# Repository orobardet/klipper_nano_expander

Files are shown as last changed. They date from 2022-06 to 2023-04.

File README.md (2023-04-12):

# Klipper Nano Expander

An Arduino Nano Shield to use with Klipper 3D printer firmware, as a auxiliary MCU.

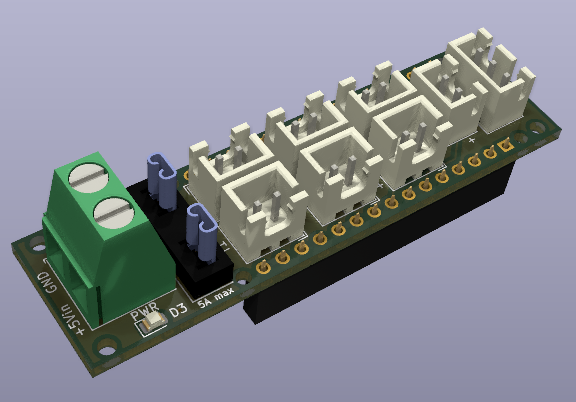
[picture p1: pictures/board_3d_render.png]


## Features

- Only require an Arduino Nano
- +5V optional external power supply with fuse
  - Connected to the Arduino Nano 5V
  - Only required if you need more than 500mA power, else the Nano power supply should be enough
- x4 temperature sensors (or any analog device as input)
- x3 PWM mosfet driven port (or any PWM controlled device as output)
- x1 Neopixel (external 5V power supply needed)

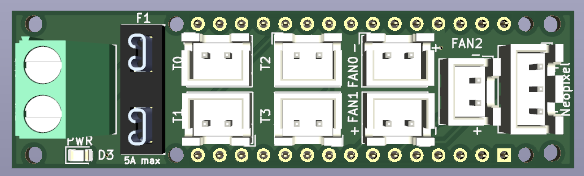
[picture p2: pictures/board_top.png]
  
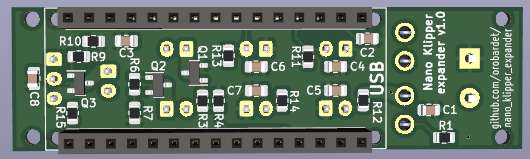
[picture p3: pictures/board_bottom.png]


- [Schematic](Schematic.pdf)
- [Mechanical drawing](Dimensions.pdf)

Source files:
- Kicad 6 project, schematic, PCB and library
- [CAD files](CAD/), including .STEP and Fusion 360 source

## Why

- Adds more temperature sensors and fan controllers
- Drives 5V fans
- Drives a 5V Neopixel without a level shifter
- Arduino nano are cheap
- Arduino nano are easy to source
- A lot of people (including me) have some in their drawers
- This board only have simple components easy to find
- Small footprint
- Does not need any hardware interaction to flash (no boot jumper or boot button to press)

## How to build

[production directory](production/) contains Gerber file and BOM + Position file for JLCPCB assembly.

If you use JLC PCB to produce and assemble your board, configure PCBA for the bottom side, where most of the SMD
component are placed.  
You'll have to solder by yourself the power indicator LED on the front of the board. It's a 0805, that can be soldered by hand.  
However this LED is not mandatory for the board to work, you can skip soldering it if you want.  
You'll also have to source and solder all the other non-SMD components:
- x2 15 pins female dupont header for the Arduino Nano (or directly the male pin of the Nano, which is not recommended)
- x1 [Keystone 3544-2 mini fuse holder](https://www.digikey.com/en/products/detail/keystone-electronics/3544-2/316029)
- x7 2 pins JST connector (FANx and THx headers)
- x1 3 pins JST connector (Neopixel headers)
- x1 screw terminal pitch 5.08mm for power in

### BOM

- [Interactive BOM](http://htmlpreview.github.io/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)
- [CSV](Klipper_nano_expander-BOM.csv) or [XLSX](Klipper_nano_expander-BOM.xlsx) BOM

Ref                | Qty | Value          | Description                                              | Soldering     | Footprint         | LCSC Ref
-------------------|-----|----------------|----------------------------------------------------------|---------------|-------------------|------------
C1, C8             |   2 | 10uF	          | Unpolarized ceramic capacitor                            | PCBA          | 0805              | [C17024](https://lcsc.com/product-detail/Multilayer-Ceramic-Capacitors-MLCC-SMD-SMT_Samsung-Electro-Mechanics-CL21A106KPFNNNE_C17024.html)
C2, C3             |   2 | 0.1uF          | Unpolarized ceramic capacitor                            | PCBA          | 0805              | [C49678](https://lcsc.com/product-detail/Multilayer-Ceramic-Capacitors-MLCC-SMD-SMT_YAGEO-CC0805KRX7R9BB104_C49678.html)
C4, C5, C6, C7     |   4 | 4.7uF          | Unpolarized ceramic capacitor                            | PCBA          | 0805              | [C1779](https://lcsc.com/product-detail/Multilayer-Ceramic-Capacitors-MLCC-SMD-SMT_Samsung-Electro-Mechanics-CL21A475KAQNNNE_C1779.html)
Q1, Q2, Q3         |   3 | IRLML6344TRPBF | MOSFET N-CH 30V 5A SOT23                                 | PCBA          | SOT-23            | [C20917](https://lcsc.com/product-detail/MOSFETs_Alpha-Omega-Semicon-AO3400A_C20917.html)
R1                 |   1 | 1K             | Resistor                                                 | PCBA          | 0805              | [C17513](https://lcsc.com/product-detail/Chip-Resistor-Surface-Mount_UNI-ROYAL-Uniroyal-Elec-0805W8F1001T5E_C17513.html)
R3, R6, R9, R15    |   4 | 100            | Resistor                                                 | PCBA          | 0805              | [C17408](https://lcsc.com/product-detail/Chip-Resistor-Surface-Mount_UNI-ROYAL-Uniroyal-Elec-0805W8F1000T5E_C17408.html)
R4, R7, R10        |   3 | 10K            | Resistor                                                 | PCBA          | 0805              | [C17414](https://lcsc.com/product-detail/Chip-Resistor-Surface-Mount_UNI-ROYAL-Uniroyal-Elec-0805W8F1002T5E_C17414.html)
R11, R12, R13, R14 |   4 | 4.7K           | Resistor                                                 | PCBA          | 0805              | [C17673](https://lcsc.com/product-detail/Chip-Resistor-Surface-Mount_UNI-ROYAL-Uniroyal-Elec-0805W8F4701T5E_C17673.html)
D3                 |   1 | Any color      | LED                                                      | PCBA          | 0805              | [C84256](https://lcsc.com/product-detail/Light-Emitting-Diodes-LED_Foshan-NationStar-Optoelectronics-NCD0805R1_C84256.html)
A1                 |   1 |                | Arduino Nano v3.x                                        | Hand-soldered |                   |
A1-a, A1-b         |   2 |                | 15 pins female dupont header + 15 mins mal dupont header | Hand-soldered | P2.54             |
F1                 |   1 | Fuse           | Mini fuse holder + 2A or 5A mini fuse                    | Hand-soldered | 3544-2_FuseHolder | 	
J1                 |   1 |                | Screw terminal 2 pins P5.08mm                            | Hand-soldered | P5.08mm           | 
FAN0, FAN1, FAN2   |   3 |                | JST 2 pins P2.54mm                                       | Hand-soldered | P2.54             | 
T0, T1, T2, T3     |   4 |                | JST 2 pins P2.54mm                                       | Hand-soldered | P2.54             | 
Neopixel           |   1 |                | JST 3 pins P2.54mm                                       | Hand-soldered | P2.54             | 

## How to use

**ONLY** use **5V** power supply! The Vin of the bord is connected to the 5V of the Arduino Nano, with no protection:  
any power >5V may fry your Nano, and any power <5V may fry you power supply.

Powering on Vin with an external 5V power supply is only necessary if you device draw more current than the Nano can provide (800mA theorically, 
but with so many Nano clone out there it's safer to stick to 500mA max).
- If you only plug temperature sensors, the Nano power supply should be enough
- If you drive a fan, I'd better power the board with external power supply (most fan draws more then 500mA when they start)
- If you drive an neopixel, **powering the board with external power supply is highly recommended**

In doubt, power the board. You should already have a 5V power source if you use Klipper, to power the Pi.

FANx header are mosfet PWM output, driving the ground:
- You can use them for anything else than FAN, like LED, heater, etc. Just stick to 1A per output max.
- If the fan or whatever you drive is not 5V, just connect its ground to the Klipper Nano Expander, and its +V to any compatible power source, **but ensure that other PSU's ground is connected to the board ground!**.

### Software configuration

Once built and connected to your Klipper host, use the provided [Klipper config file](config/nano_klipper_expander.cfg).  

You need at least to set the `serial` path in the `[mcu ...]` of the provided klipper configuration file.  
To find the serial of your Arduino Nano:
- BEFORE connecting the Nano with USB on the Raspberry Pi, connect to the Pi using SSH and run the command `ls /dev/serial/by-id/`. Note the result.
- Connect the Nano with USB on the Pi, wait a few seconds for the Pi to detect the USB device, and re-run the same command as before.
- A new "file" should be there, looking like `usb-1a86_USB2.0-Serial-if00-port0`: it represents your Arduino Nano
- Change the `serial` setting value in the Klipper configuration using the full path to the serial file. e.g.: `serial: /dev/serial/by-id/usb-1a86_USB2.0-Serial-if00-port0`

Here is the pin mapping for reference:
- TH0: PC0
- TH1: PC1
- TH2: PC2
- TH3: PC3
- FAN0: PB1
- FAN1: PD5
- FAN2: PD3
- Neopixel Data: PD6

The configuration file must be included in some way into the main `printer.cfg` config filr of Klipper.

### Flashing firmware

To flash the firmware, you do not need to have the configuration file ready, but you need:
- The Nano connected to the Raspberry Pi
- The path of the serial representing the Nano on the Pi (see previous section)
- Klipper installed on the Pi
- AVR compilation package installed on the Rapsberry Pi hosting Klipper: `sudo apt install gcc-avr avr-libc avrdude binutils-avr`

To flash the Nano with Klipper:

- Connect to the Pi using SSH.
- Create a `klipper_config` directory in you home directory, if it not exists already: `mkdir -p ~/klipper_config`.
- Go the the directory containing klipper (usually: `cd ~/klipper`).
- Run `make clean KCONFIG_CONFIG=~/klipper_config/config.arduinonano`.
- Run `make menuconfig KCONFIG_CONFIG=~/klipper_config/config.arduinonano` and configure as followed, and then save'n'quit:  
  - _Enable extra low-level configuration options_: NOT checked
  - _Micro-controller Architecture_: `Atmega AVR`
  - _Processor model_: `atmega328p`   
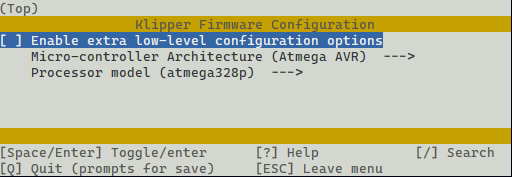
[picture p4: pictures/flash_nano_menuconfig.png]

- Run `make KCONFIG_CONFIG=~/klipper_config/config.arduinonano` to build the firmware.  
  **Note:** If the firmware compilation fails with errors like `'.data' is not within region 'data'`, you may sufffer a known bug with AVR toolchain on Debian Bullseye (check your linux distribution codename with `lsb_release -a`). If so, you can try [a workaround describe here to install a previous and non-buggy AVR toolchain](https://github.com/Klipper3d/klipper/issues/4938#issuecomment-1094246978). Once installed, re-roll the current procedure from the `make clean` step (a reboot of the Pi may be usefull between new toolchain installation and the retry).
- **Stop Klipper** if it's running (usually: `sudo systemctl stop klipper`)
- Run `make flash KCONFIG_CONFIG=~/klipper_config/config.arduinonano FLASH_DEVICE=/dev/serial/by-id/usb-1a86_USB2.0-Serial-if00-port0`, _**replacing the `FLASH_DEVICE=` value with the full path of you Nano on your Pi!**_ This will flash the firmware to the Arduino Nano.
- Start Klipper (usually: `sudo systemctl start klipper`)

If no error occurs, Klipper's firmware is now loaded into the Arduino Nano.  
You can now configure Klipper to use the Nano Expander.

### Mounting

x2 3D printable mounts are provided (STL files):
- [without mounting holes](STL/nano_expander_mount.stl): lower footprint, but require some tape (like VHB tape) to secure the mount on a flat surface.
- [with mounting holes](STL/nano_expander_mount_with_holes.stl): a wider mount with 4 mounting holes, to secure the mount with M3 screws. Screws position and distance can be found in [dimension drawing](Dimensions.pdf).

Both mounts require x4 M2x3mm screw to secure the board to the mount.

## Compatibility

Aside from Arduino Nano and its clone, this board _may_ be compatible with other MCU boards using the same form factor than the Arduino Nano, and a compatible pinout.

- [Cytron Maker Nano RP2040](config/rp2040_klipper_expander.cfg): flashing the firmware is a bit different, as it is based on the Raspberry Pi RP2040 MCU rather than an ATMega MCU. 

## Credit

Inspired by [STM32-Klipper-Expander](https://github.com/VoronDesign/Voron-Hardware/tree/master/Klipper_Expander) by Voron Design Team.  
Temperature sensors and FAN output of Klipper Nano Expander are a copy of those of STM32-Klipper-Expander.  
The Cytron Maker Nano RP2040 config is a contribution of **tehmaze** (#2).

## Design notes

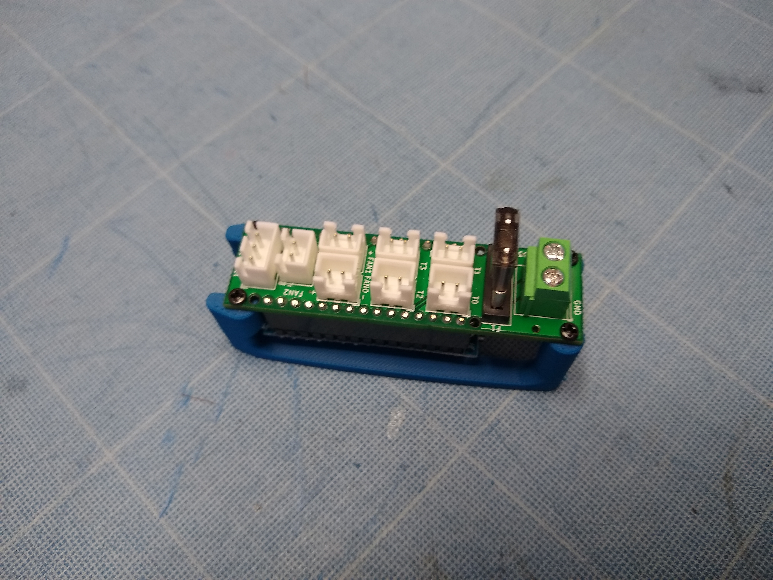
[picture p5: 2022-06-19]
pictures/klipper_nano_expander_real_full.jpg

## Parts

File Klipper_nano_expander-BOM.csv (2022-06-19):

Ref | Qty | Value | Description | Footprint | LCSC Ref
A1 | 1 |  | Arduino Nano v3.x
A1-a, A1-b | 2 |  | 15 pins female dupont header + 15 mins mal dupont header
C1, C8 | 2 | 10uF | Unpolarized ceramic capacitor | 0805 | C17024
C2, C3 | 2 | 0.1uF | Unpolarized ceramic capacitor | 0805 | C49678
C4, C5, C6, C7 | 4 | 4.7uF | Unpolarized ceramic capacitor | 0805 | C1779
D3 | 1 | Any color | LED | 0805 | C84256
F1 | 1 | Fuse | Mini fuse holder + 2A or 5A mini fuse | 3544-2_FuseHolder
Q1, Q2, Q3 | 3 | IRLML6344TRPBF | MOSFET N-CH 30V 5A SOT23 | SOT-23 | C20917
R1 | 1 | 1K | Resistor | 0805 | C17513
R3, R6, R9, R15 | 4 | 100 | Resistor | 0805 | C17408
R4, R7, R10 | 3 | 10K | Resistor | 0805 | C17414
R11, R12, R13, R14 | 4 | 4.7K | Resistor | 0805 | C17673
J1 | 1 |  | Screw terminal 2 pins P5.08mm | P5.08mm
FAN0, FAN1, FAN2 | 3 |  | JST 2 pins P2.54mm | P2.54
T0, T1, T2, T3 | 4 |  | JST 2 pins P2.54mm | P2.54
Neopixel | 1 |  | JST 3 pins P2.54mm | P2.54

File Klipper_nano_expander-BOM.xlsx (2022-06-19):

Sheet: Klipper nano expander BOM
Ref | Qty | Value | Description | Footprint | LCSC Ref
A1 | 1 |  | Arduino Nano v3.x
A1-a, A1-b | 2 |  | 15 pins female dupont header + 15 mins mal dupont header
C1, C8 | 2 | 10uF | Unpolarized ceramic capacitor | 0805 | C17024
C2, C3 | 2 | 0.1uF | Unpolarized ceramic capacitor | 0805 | C49678
C4, C5, C6, C7 | 4 | 4.7uF | Unpolarized ceramic capacitor | 0805 | C1779
D3 | 1 | Any color | LED | 0805 | C84256
F1 | 1 | Fuse | Mini fuse holder + 2A or 5A mini fuse | 3544-2_FuseHolder
Q1, Q2, Q3 | 3 | IRLML6344TRPBF | MOSFET N-CH 30V 5A SOT23 | SOT-23 | C20917
R1 | 1 | 1K | Resistor | 0805 | C17513
R3, R6, R9, R15 | 4 | 100 | Resistor | 0805 | C17408
R4, R7, R10 | 3 | 10K | Resistor | 0805 | C17414
R11, R12, R13, R14 | 4 | 4.7K | Resistor | 0805 | C17673
J1 | 1 |  | Screw terminal 2 pins P5.08mm | P5.08mm
FAN0, FAN1, FAN2 | 3 |  | JST 2 pins P2.54mm | P2.54
T0, T1, T2, T3 | 4 |  | JST 2 pins P2.54mm | P2.54
Neopixel | 1 |  | JST 3 pins P2.54mm | P2.54

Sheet: Klipper nano expander
Ref,"Qnty","Value","Cmp name","Footprint","Description","Vendor"
A1, ,"1","Arduino_Nano_v3.x","Arduino_Nano_v3.x","Module:Arduino_Nano_WithMountingHoles","Arduino Nano v3.x",""
C1, C8, ,"2","10uF","C","Capacitor_SMD:C_0805_2012Metric","Unpolarized capacitor",""
C2, C3, ,"2","0.1uF","C","Capacitor_SMD:C_0805_2012Metric","Unpolarized capacitor",""
C4, C5, C6, C7, ,"4","4.7uF","C","Capacitor_SMD:C_0805_2012Metric","Unpolarized capacitor",""
D3, ,"1","LED","LED","LED_SMD:LED_0805_2012Metric","Light emitting diode",""
F1, ,"1","Fuse","Fuse","local:3544-2_FuseHolder","Fuse",""
FAN0, FAN1, FAN2, ,"3","Conn_01x02","Conn_01x02","Connector_JST:JST_XH_B2B-XH-A_1x02_P2.50mm_Vertical","Generic connector, single row, 01x02, script generated (kicad-library-utils/schlib/autogen/connector/)",""
H1, H2, H3, H4, ,"4","MountingHole","MountingHole","MountingHole:MountingHole_2mm","Mounting Hole without connection",""
J1, ,"1","+5Vin","Screw_Terminal_01x02","TerminalBlock_Phoenix:TerminalBlock_Phoenix_MKDS-1,5-2-5.08_1x02_P5.08mm_Horizontal","Generic screw terminal, single row, 01x02, script generated (kicad-library-utils/schlib/autogen/connector/)",""
J2, ,"1","Conn_01x03","Conn_01x03","Connector_JST:JST_XH_B3B-XH-A_1x03_P2.50mm_Vertical","Generic connector, single row, 01x03, script generated (kicad-library-utils/schlib/autogen/connector/)",""
Q1, Q2, Q3, ,"3","IRLML6344TRPBF","IRLML6344TRPBF","Package_TO_SOT_SMD:SOT-23","MOSFET N-CH 30V 5A SOT23",""
R1, ,"1","1K","R","Resistor_SMD:R_0805_2012Metric","Resistor",""
R3, R6, R9, R15, ,"4","100","R","Resistor_SMD:R_0805_2012Metric","Resistor",""
R4, R7, R10, ,"3","10K","R","Resistor_SMD:R_0805_2012Metric","Resistor",""
R11, R12, R13, R14, ,"4","4.7K","R","Resistor_SMD:R_0805_2012Metric","Resistor",""
T0, T1, T2, T3, ,"4","Conn_01x02","Conn_01x02","Connector_JST:JST_XH_B2B-XH-A_1x02_P2.50mm_Vertical","Generic connector, single row, 01x02, script generated (kicad-library-utils/schlib/autogen/connector/)",""

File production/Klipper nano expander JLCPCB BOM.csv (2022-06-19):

Comment | Designator | Footprint | LCSC
Arduino_Nano_v3.x | A1 | Module:Arduino_Nano_WithMountingHoles
10uF | C1,C8 | Capacitor_SMD:C_0805_2012Metric | C17024
0.1uF | C2,C3 | Capacitor_SMD:C_0805_2012Metric | C49678
4.7uF | C4,C5,C6,C7 | Capacitor_SMD:C_0805_2012Metric | C1779
LED | D3 | LED_SMD:LED_0805_2012Metric | C84256
Fuse | F1 | local:3544-2_FuseHolder
Conn_01x02 | FAN0,T0,FAN1,T1,FAN2,T2,T3 | Connector_JST:JST_XH_B2B-XH-A_1x02_P2.50mm_Vertical
MountingHole | H1,H2,H3,H4 | MountingHole:MountingHole_2mm
+5Vin | J1 | TerminalBlock_Phoenix:TerminalBlock_Phoenix_MKDS-1,5-2-5.08_1x02_P5.08mm_Horizontal
Conn_01x03 | J2 | Connector_JST:JST_XH_B3B-XH-A_1x03_P2.50mm_Vertical
IRLML6344TRPBF | Q1,Q2,Q3 | Package_TO_SOT_SMD:SOT-23 | C20917
1K | R1 | Resistor_SMD:R_0805_2012Metric | C17513
4.7K | R11,R12,R13,R14 | Resistor_SMD:R_0805_2012Metric | C17673
100 | R3,R6,R9,R15 | Resistor_SMD:R_0805_2012Metric | C17408
10K | R4,R7,R10 | Resistor_SMD:R_0805_2012Metric | C17414

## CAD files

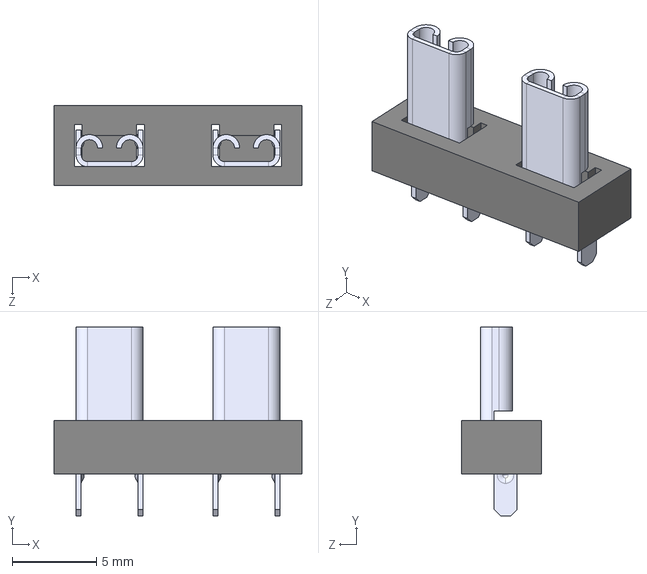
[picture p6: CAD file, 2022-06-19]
3d_models/3544-2_FuseHolder.STEP
14.7 x 11.2 x 4.75 mm

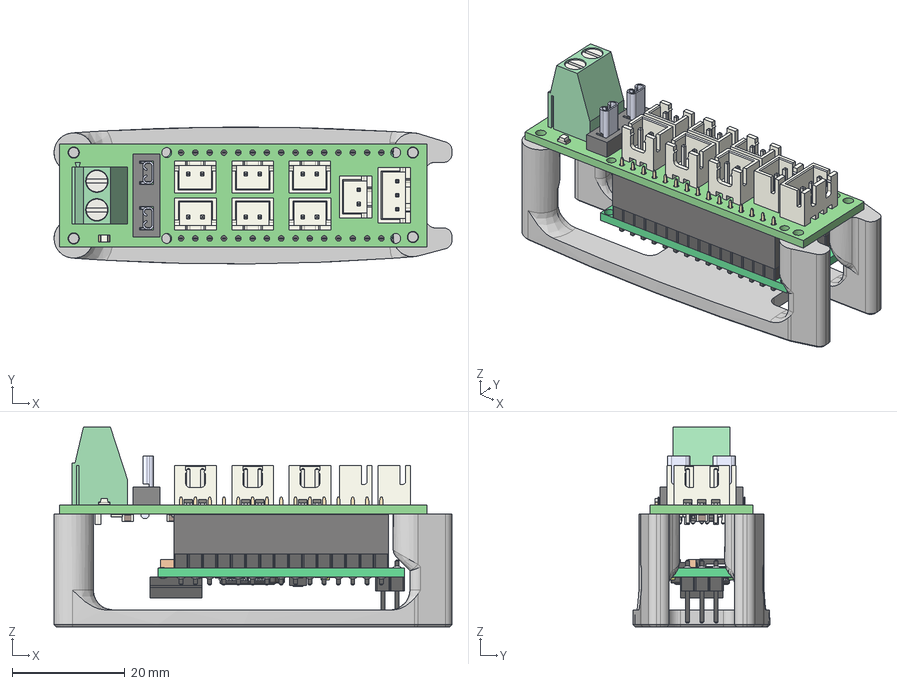
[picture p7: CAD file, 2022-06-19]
CAD/Klipper Nano expander mount.step
70.6 x 24.3 x 35.5 mm
Klipper nano expander PCB
switch
Led x 3
Led (1)
Pin x 21
chip1
USB
Crystal
Pin (1) x 15
Res x 5
cap x 2
Chip
respack x 2
diode
vreg
nano_expander_mount

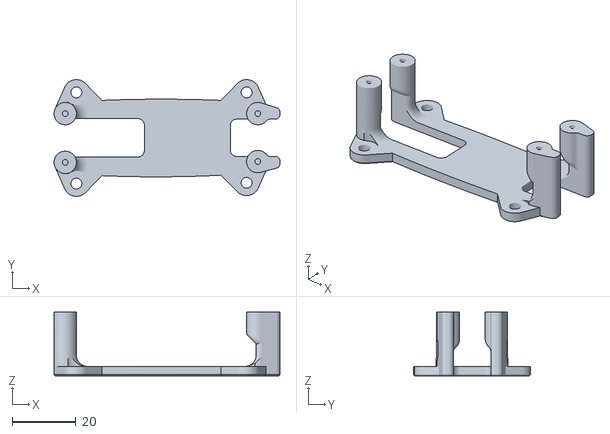
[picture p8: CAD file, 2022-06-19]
STL/nano_expander_mount_with_holes.stl
70.6 x 36.5 x 20.0

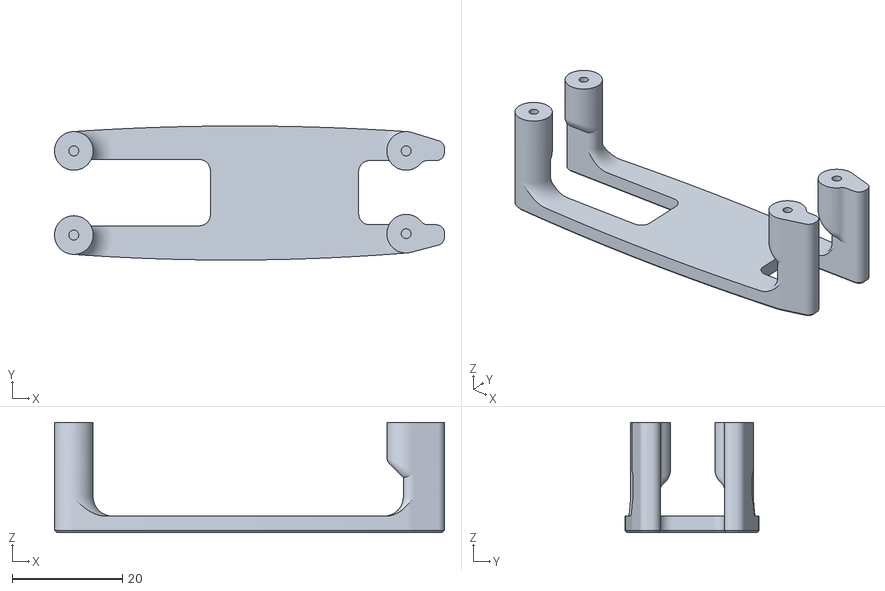
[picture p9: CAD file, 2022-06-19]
STL/nano_expander_mount.stl
70.6 x 24.3 x 20.0

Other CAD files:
CAD/Klipper Nano expander mount.f3z

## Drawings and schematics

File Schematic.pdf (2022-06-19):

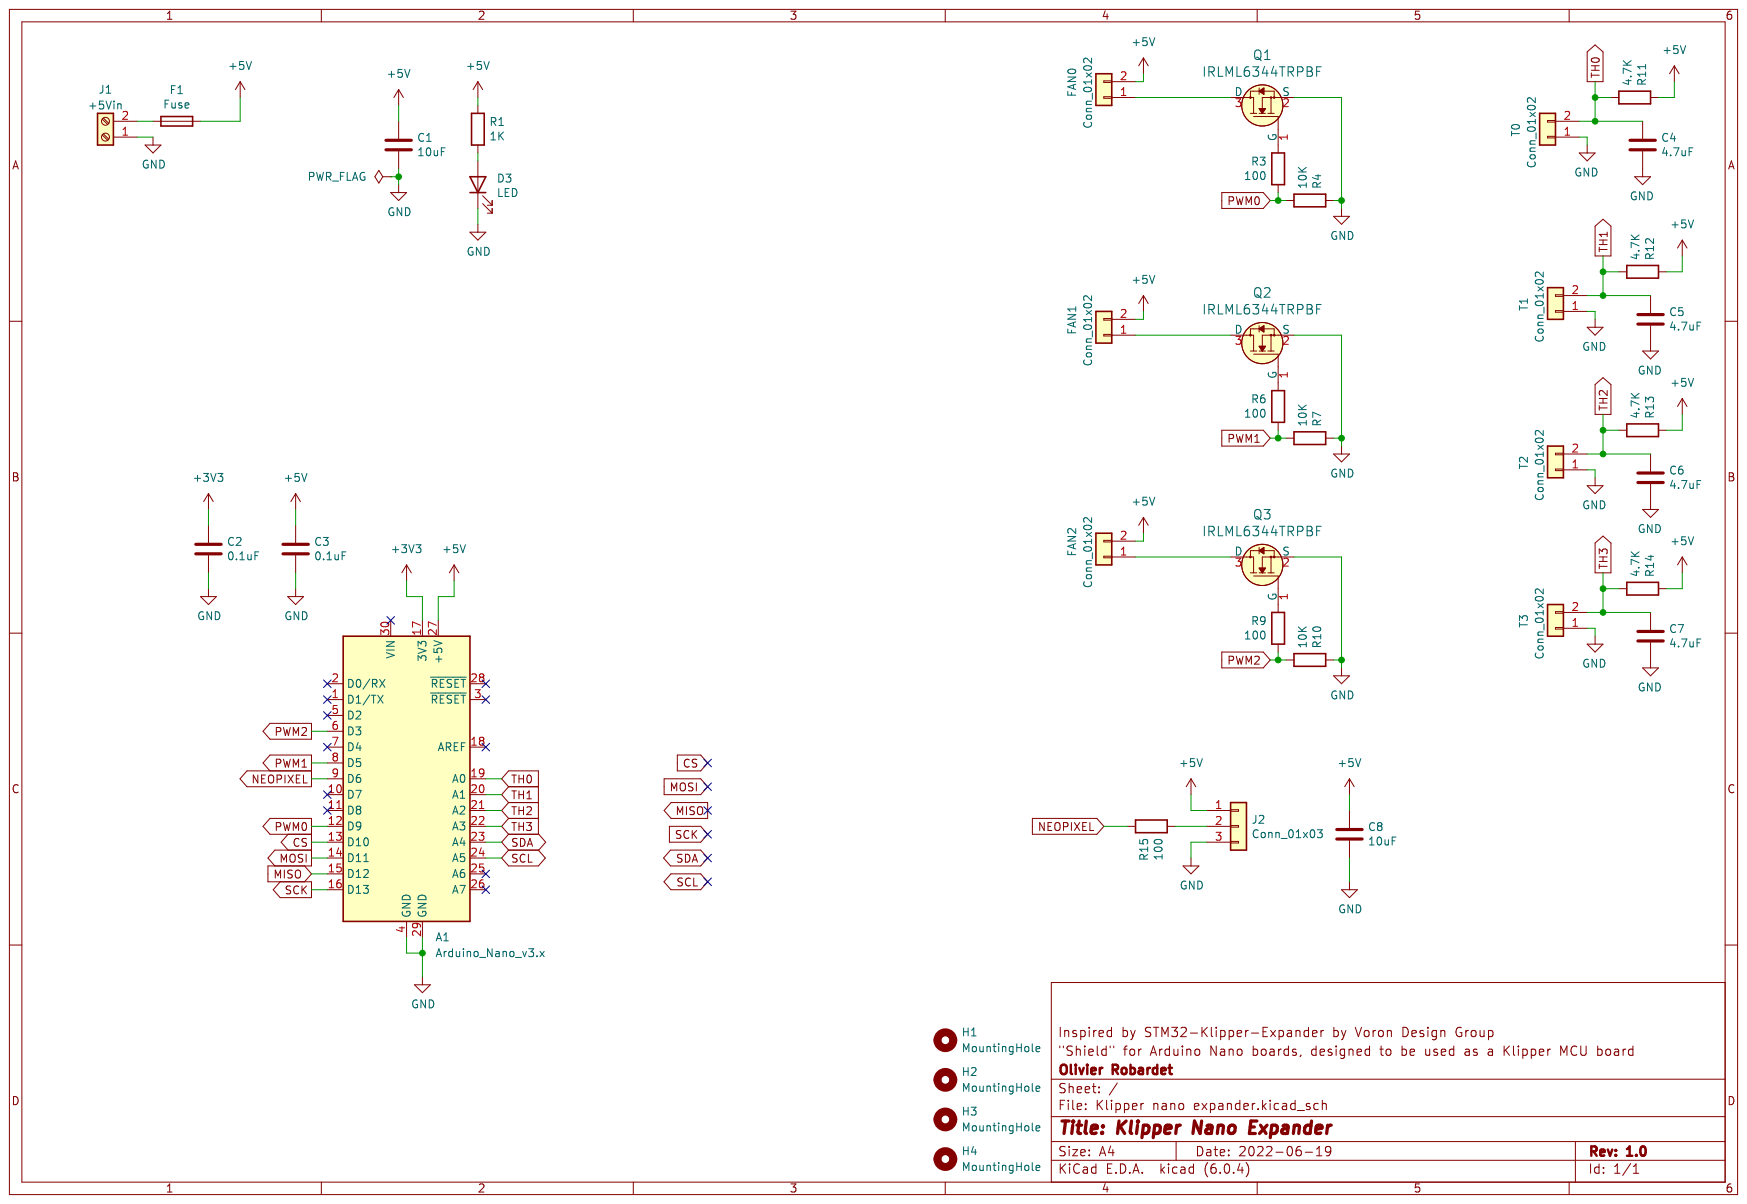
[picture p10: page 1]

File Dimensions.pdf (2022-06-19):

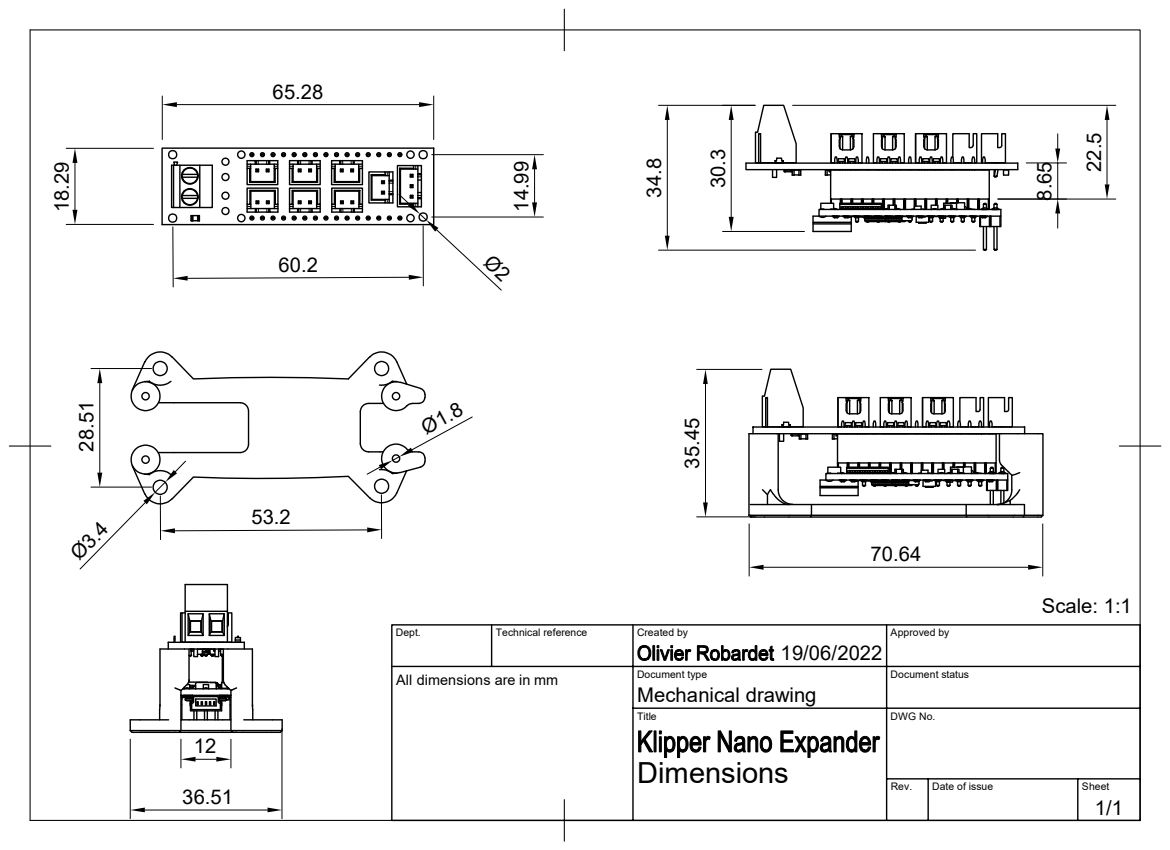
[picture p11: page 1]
Dept.; Technical reference; Created by; Approved by Document type; Document status Title; DWG No. Rev.; Date of issue; Sheet Mechanical drawing 19/06/2022; 1/1 Dimensions ⁶⁵.28

Ø2 Scale: 1:1 All dimensions are in mm

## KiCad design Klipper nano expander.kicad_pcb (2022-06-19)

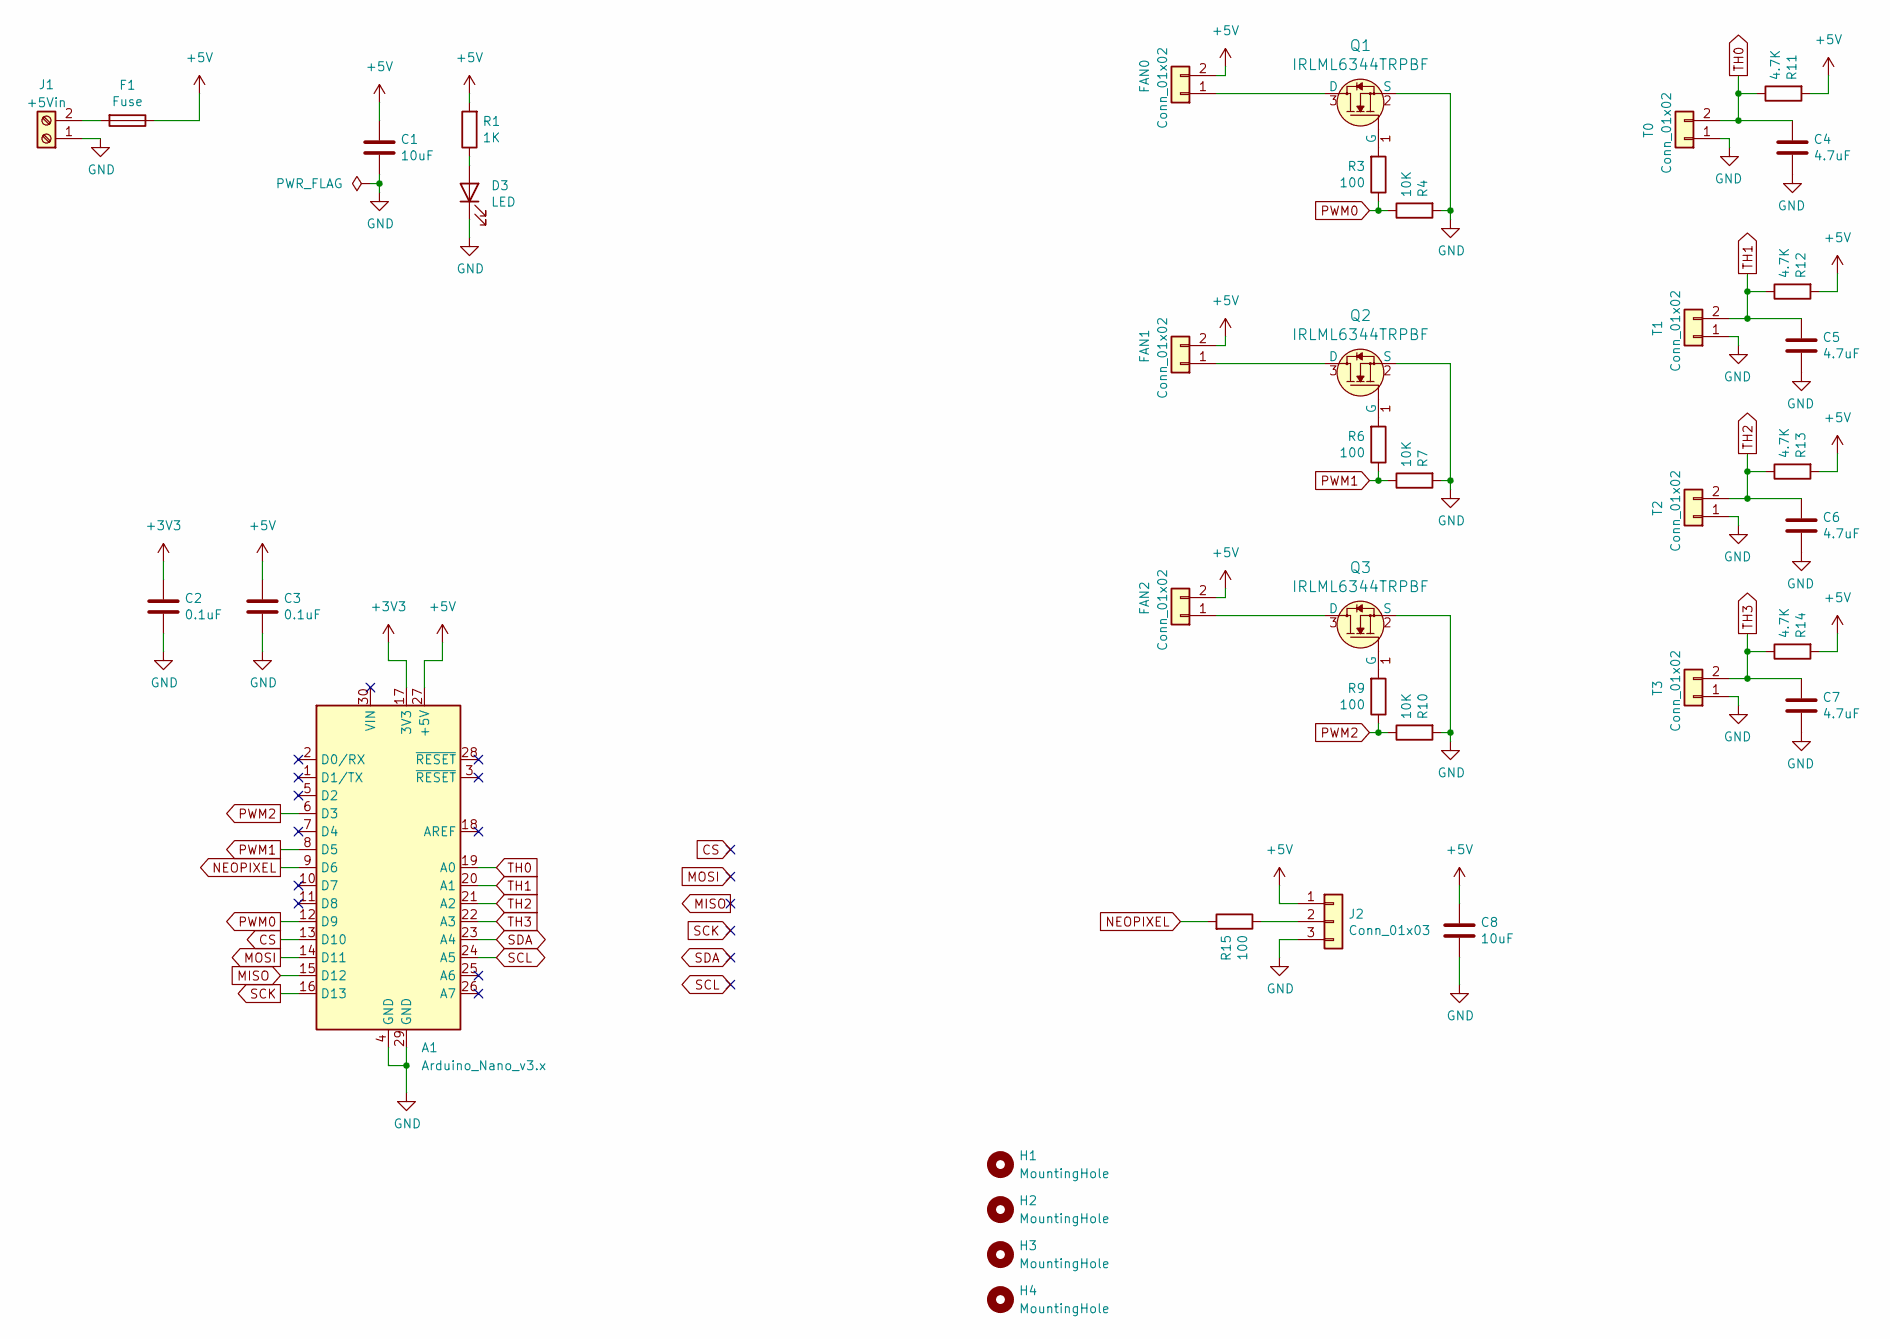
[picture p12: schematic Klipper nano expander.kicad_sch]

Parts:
A1: Arduino_Nano_v3.x; Arduino_Nano_WithMountingHoles
C1, C8: 10uF; C_0805_2012Metric; MPN CL21A106KPFNNNE; LCSC C17024
C2, C3: 0.1uF; C_0805_2012Metric; MPN CC0805KRX7R9BB104; LCSC C49678
C4, C5, C6, C7: 4.7uF; C_0805_2012Metric; MPN CC0805KKX5R8BB475; LCSC C1779
D3: LED; LED_0805_2012Metric; MPN 17-215SURC/S530-A2/TR8; LCSC C84256
F1: Fuse; 3544-2_FuseHolder
FAN0, FAN1, FAN2: Conn_01x02; JST_XH_B2B-XH-A_1x02_P2.50mm_Vertical
H1, H2, H3, H4: MountingHole; MountingHole_2mm
J1: +5Vin; TerminalBlock_Phoenix_MKDS-1,5-2-5.08_1x02_P5.08mm_Horizont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
J2: Conn_01x03; JST_XH_B3B-XH-A_1x03_P2.50mm_Vertical
Q1, Q2, Q3: IRLML6344TRPBF; SOT-23; MPN IRLML6344TRPBF; Digi-Key_PN IRLML6344TRPBFCT-ND
R1: 1K; R_0805_2012Metric; MPN RC0805JR-071KL; LCSC C17513
R3, R6, R9, R15: 100; R_0805_2012Metric; MPN RC0805JR-07100RL; LCSC C17408
R4, R7, R10: 10K; R_0805_2012Metric; MPN RC0805JR-0710KL; LCSC C17414
R11, R12, R13, R14: 4.7K; R_0805_2012Metric; MPN RC0805JR-074K7L; LCSC C17673
T0, T1, T2, T3: Conn_01x02; JST_XH_B2B-XH-A_1x02_P2.50mm_Vertical

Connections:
+3V3: A1.17 (3V3), C2.2
+5V: A1.27 (+5V), C1.2, C3.2, C8.2, F1.1, FAN0.2, FAN1.2, FAN2.2, J2.1, R1.2, R11.2, R12.2, R13.2, R14.2
CS: A1.13 (D10)
GND: A1.4 (GND), A1.29 (GND), C1.1, C2.1, C3.1, C4.1, C5.1, C6.1, C7.1, C8.1, D3.1 (K), J1.1, J2.3, Q1.2 (S), Q2.2 (S), Q3.2 (S), R4.2, R7.2, R10.2, T0.1, T1.1, T2.1, T3.1
MISO: A1.15 (D12)
MOSI: A1.14 (D11)
NEOPIXEL: A1.9 (D6), R15.2
unnamed: D3.2 (A), R1.1
unnamed: F1.2, J1.2
unnamed: FAN0.1, Q1.3 (D)
unnamed: FAN1.1, Q2.3 (D)
unnamed: FAN2.1, Q3.3 (D)
unnamed: J2.2, R15.1
unnamed: Q1.1 (G), R3.2
unnamed: Q2.1 (G), R6.2
unnamed: Q3.1 (G), R9.2
PWM0: A1.12 (D9), R3.1, R4.1
PWM1: A1.8 (D5), R6.1, R7.1
PWM2: A1.6 (D3), R9.1, R10.1
SCK: A1.16 (D13)
SCL: A1.24 (A5)
SDA: A1.23 (A4)
TH0: A1.19 (A0), C4.2, R11.1, T0.2
TH1: A1.20 (A1), C5.2, R12.1, T1.2
TH2: A1.21 (A2), C6.2, R13.1, T2.2
TH3: A1.22 (A3), C7.2, R14.1, T3.2

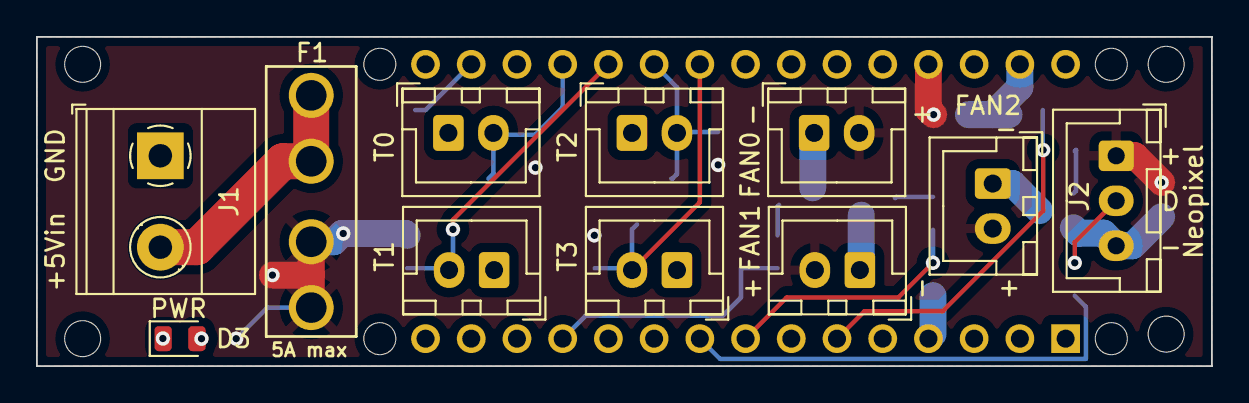
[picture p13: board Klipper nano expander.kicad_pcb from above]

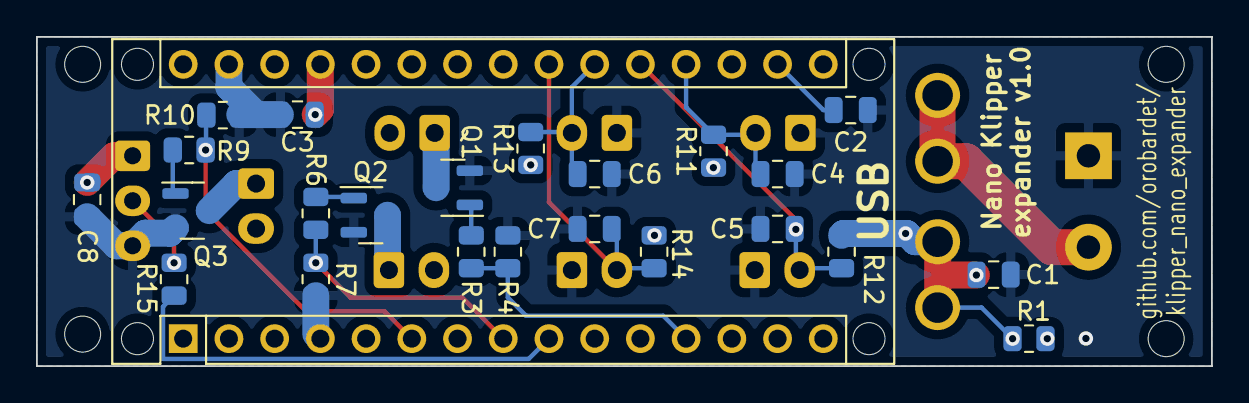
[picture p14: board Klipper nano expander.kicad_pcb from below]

Board: 2 copper layers, 65.3 x 18.3 mm, 39 parts (24 on the bottom side), 20 nets.

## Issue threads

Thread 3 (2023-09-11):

Only 5V fan?

za-x-az, 2023-09-11:
Is it correct that this is only for 5V fans?

I was looking for just a board like this, but for 12/24v fans.

orobardet, 2023-09-12:
Hi,
Yes, it's 5V only, there is no regulator on the board. It was design for this purpose: having auxiliary Kilipper MCUs capable of driving 5V devices.

For 12/24V, you may want to use the [Klipper Expander](https://github.com/VoronDesign/Voron-Hardware/tree/master/Klipper_Expander).

za-x-az, 2023-09-12:
Sadly I'm looking for something more or less like your board, but for
12/24V :)
Thx for the fast answer i will keep looking

On Tue, 12 Sept 2023 at 08:32, Olivier Robardet ***@***.***>
wrote:

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

--
M.v.h. / Best Regards

Andreas L. Rasmussen

Closed 2024-05-17.

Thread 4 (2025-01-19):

Collect2 error

jStrahan73, 2025-01-19:
When I try to make the elf file I get this error

Collect2: error: ld returned 1 exit status
Makefile 73 out/klipper.elf error 1

orobardet, 2025-01-21:
Hi @jStrahan73,

On what hardware and Operating System are you trying to build the firmware? If using a debian-based OS bookworm or latter, did you see in the README and apply the workaround for the AVR toolchain? (https://github.com/Klipper3d/klipper/issues/4938#issuecomment-1094246978)

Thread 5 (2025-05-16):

Thermistor Pullup resistor should connect to +3.3V, not 5V

kpt-smirk, 2025-05-16:
The pullup resistor (4k7ohm) should connect to the 3v3 Power level, not to the  5v
I use the board with the maker nano RP2040 and i read completely wrong temperatures,

kpt-smirk, 2025-05-16:
In the scheme it's R11 ... R14

orobardet, 2025-05-16:
Hi.
Thanks for your report, but this board was designed on purpose for **5V** Arduino Nano, which use an ATmega328.
So, it's expected it does not work correctly on a 3.3V RP2040 MCU. It's by design.

Closed 2025-05-16.

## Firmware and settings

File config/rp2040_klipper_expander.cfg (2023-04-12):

# Configuration for the Cytron Maker Nano RP2040
#
# This board has two NeoPixels on GPIO11, a beeper on GPIO22 and a bunch of 
# individually controllable LEDs on GPIO12-15.

[mcu expander]
serial: /dev/serial/by-id/usb-Klipper_rp2040_XXXXXXXXXXXX-if00

[neopixel expander_leds]
pin:         expander:gpio11
chain_count: 2
color_order: GRB

[output_pin expander_beeper]
pin:         expander:gpio22
pwm:         True
value:       0
shutdown_value: 0
cycle_time:  0.001

[temperature_sensor expander]
sensor_type: temperature_mcu
sensor_mcu:  expander

[temperature_sensor TH0]
sensor_pin:  expander:gpio26
sensor_type: Generic 3950

#[temperature_sensor TH1]
#sensor_pin:  expander:gpio27
#sensor_type: Generic 3950

#[temperature_sensor TH2]
#sensor_pin:  expander:gpio28
#sensor_type: Generic 3950

#[temperature_sensor TH3]
#sensor_pin:  expander:gpio29
#sensor_type: Generic 3950

[fan_generic FAN0]
pin:         expander:gpio9
max_power:   1.0

#[fan_generic FAN1]
#pin:         expander:gpio5
#max_power:   1.0
#
#[fan_generic FAN2]
#pin:         expander:gpio3
#max_power:   1.0

[gcode_macro M300]
gcode:
  # Use a default 1kHz tone if S is omitted.
    {% set S = params.S|default(1000)|int %}
    # Use a 10ms duration is P is omitted.
    {% set P = params.P|default(100)|int %}
    SET_PIN PIN=expander_beeper VALUE=0.5 CYCLE_TIME={ 1.0/S if S > 0 else 1 }
    G4 P{P}
    SET_PIN PIN=expander_beeper VALUE=0

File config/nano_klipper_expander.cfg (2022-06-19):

[mcu nano_expander]
# CHANGE THE SERIAL!
serial: /dev/serial/by-id/usb-xxx
restart_method: arduino

# TH0
[temperature_sensor TH0]
sensor_pin: nano_expander:PC0
sensor_type: Generic 3950

# # TH1
# [temperature_sensor TH1]
# sensor_pin: nano_expander:PC1

# # TH2
# [temperature_sensor TH2]
# sensor_pin: nano_expander:PC2

# # TH3
# [temperature_sensor TH3]
# sensor_pin: nano_expander:PC3

# FAN0
[fan_generic FAN0]
pin: nano_expander:PB1
max_power: 1.0

# # FAN1
# [fan_generic FAN1]
# pin: nano_expander:PD5
# max_power: 1.0

# # FAN2
# [fan_generic FAN2]
# pin: nano_expander:PD3
# max_power: 1.0

# Neopixel
[neopixel nano_expander_neopixel]
pin: nano_expander:PD6
chain_count: 3
initial_RED: 1.0
initial_GREEN: 1.0
initial_BLUE: 1.0

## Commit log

2022-06-19 Fix interactive BOM link
2022-07-05 Fix screw terminal pitch in description
    And some type
2023-04-11 Create rp2040_klipper_expander.cfg
    Reference configuration for the Cytron Maker Nano RP2040, for those looking to use a Pi Pico (rev B2) RP2040 micro controller, rather than the Arduino ATMega series.
    [rp2040_klipper_expander.cfg]
2023-04-12 Add alternative MCU boards and Cytron Maker Nano RP2040
